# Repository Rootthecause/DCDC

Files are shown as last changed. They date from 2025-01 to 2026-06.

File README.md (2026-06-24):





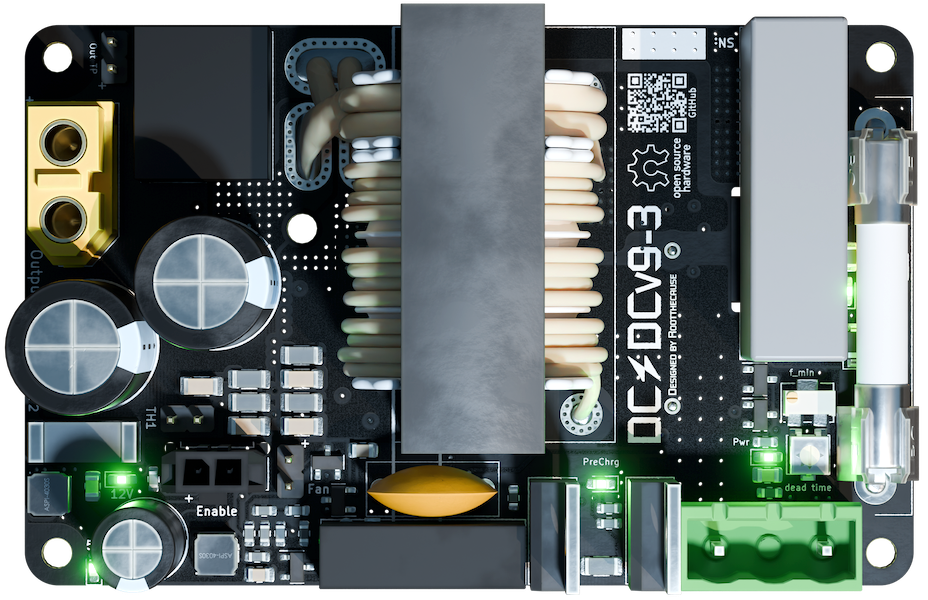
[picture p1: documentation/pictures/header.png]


Dear Formula Student Teams,

I've designed a High Voltage DC/DC Converter to replace our LV Battery. Feel free to use it as well!<br>
Although this design (and previous versions) have passed two times FSG scrutineering and have been operating without any issues for over 6 months, <strong>always manufacture at your own risk!</strong><br>
If you encountered any bugs or have suggestions for improvement, please use the GitHub [issues form](https://github.com/Rootthecause/DCDC/issues/new). For discussions and technical questions, kindly use the [discussion bord](https://github.com/Rootthecause/DCDC/discussions).<br> 

This design is published as open-source hardware under the CERN-OHL-W license and can be found on GitHub: https://github.com/Rootthecause/DCDC<br>
If you had early access to this GitHub page or received any files from me directly, please do not share or publish them, as I don't want others to share files which may be incomplete or contain errors.<br>

Have fun! Do not lick things with spark symbols on :) 

Best regards,
Rootthecause / Liv 

March 10, 2026: Thanks for giving this repro more than 100 stars! ⭐️
<br>

# Updates
### For recent updates on building a v9-3 replica, please read [the v9-3 Build Notes](https://github.com/Rootthecause/DCDC/blob/main/v9-3_build_notes.md).

|Date YYMMDD| Description |
|:---:|:---|
|260609| Added new [v9-4_dev](https://github.com/Rootthecause/DCDC/tree/v9-4_dev) branch. This version is currently untested and not recommended for use. Some components were improved, like D14, U1, U11, Q8, Q9, Q10, Q11. SR FETs have more vias and 20% larger cooling surface. Increased TS side control voltage from 12V to 15V for lower conduction losses.|
|260326 | Update on [v10 development](https://github.com/Rootthecause/DCDC/discussions/9#discussioncomment-16319278) currently being slowed down due to transformer issues |
|260314| Release of the v9-3r1.4 update. Fixes many smaller issues and probably issue #10. See [releases](https://github.com/Rootthecause/DCDC/releases) for more details.|
|260129| First public v10 schematic, see [v10 development](https://github.com/Rootthecause/DCDC/discussions/9#discussioncomment-15634156), also contains a timeline and small v9-3 update|
|260104| New year's update on [v10 development](https://github.com/Rootthecause/DCDC/discussions/9#discussioncomment-15400450) |
|251130| Update on [v10 development](https://github.com/Rootthecause/DCDC/discussions/9#discussioncomment-15114408), added  for faster communication.|
|250915| **IMPORTANT NOTICE**: There was a complaint about the converter not being rules conform. Due to other personal priorities it might take some weeks to solve the addressed points. There is also the chance of some points unable to be resolved for the Version 9-3r. See [issue#10](https://github.com/Rootthecause/DCDC/issues/10) for further details.|
|250806| Announcing the v10 development - ideas welcome! Read more [here](https://github.com/Rootthecause/DCDC/discussions/9). DCDCv10 [survey](https://forms.gle/ou8AZbYJj4cU9K3A8).|
|250718| A bad F_min setting lead to repeatable FET destruction, please re-read the Build Guide Pages 35/36 if you've set up your replica before this change. See [issue#8](https://github.com/Rootthecause/DCDC/issues/8) |
<br>

# Important documents
|File | | |
|:---:|:---:|:---:|
| Documentation [PDF] | [ENGLISH](https://github.com/Rootthecause/DCDC/blob/main/documentation/Documentation_DCDCv9-3r_EN.pdf)| [GERMAN](https://github.com/Rootthecause/DCDC/blob/main/documentation/Documentation_DCDCv9-3r_GER.pdf) [Discontinued*]|
| Build Guide [PDF] | [ENGLISH](https://github.com/Rootthecause/DCDC/blob/main/documentation/Build_Guide_DCDCv9-3r_EN.pdf)| [GERMAN](https://github.com/Rootthecause/DCDC/blob/main/documentation/Build_Guide_DCDCv9-3r_GER.pdf) [Discontinued*]|
| Data sheet [PDF] | [ENGLISH](https://github.com/Rootthecause/DCDC/blob/main/documentation/Datasheet_DCDCv9-3.pdf)|-|
| KiCAD Files| [ENGLISH](https://github.com/Rootthecause/DCDC/tree/main/kicad)|-|
| Schematic [PDF] | [ENGLISH](https://github.com/Rootthecause/DCDC/blob/main/kicad/DCDCv9-3.pdf) |-|
| LTspice Simulation| [ENGLISH](https://github.com/Rootthecause/DCDC/tree/main/ltspice)|-|
| Measurements Table [xlsx] | [ENGLISH](https://github.com/Rootthecause/DCDC/blob/main/documentation/DCDCv9-3_Table.xlsx) |-|
| Scrutineering Support Presentation [PPTX] | [ENGLISH](https://github.com/Rootthecause/DCDC/blob/main/documentation/scrutineering_support_files/DCDCv9-3_Scrutineering_Support_Presentation.pptx)|-|

*will not be updated after the DCDCv9-3r1.4 release (March 14, 2026).

<br>

# Note for PCB-Orders
**Always check the latest release before ordering!**
There are new releases for every significant hardware change.
I do not recommend ordering from the latest repro clone, as it might contain unfinished hardware changes. However, simulation files or documents might be more recent.
<br>
<br>
# Who should build this?
This project is for anyone who is keen to build a DC/DC converter for powering low voltage devices from high voltages or for research.
Unfortunately, it's currently not a simple one-day-build (maybe 1-2 days for building and 1-2 Weeks for testing), but I'm working on it, making it as accessible as possible.
The skillset required ranges from soldering SMD components, SLA-Printing to sanding ferrite cores and winding a transformer (sanding is currently not needed anymore).
The documentation not only contains explanations of many components, but also detailed written assembly instructions.
I might also record a few instruction videos if there is a demand.
Stick with it - the results speak for themselves.<br>
<br>
# Technical Specifications

The DCDCv9-3 is a galvanically isolated DC/DC converter, designed to convert voltages from 200 V to 600 V down to 24 V with max. 500 W continuous output power. The low weight of 167 grams and the small footprint of a credit card (85.6 x 54 mm) are well suited to the automotive industry for supplying low-voltage systems from HV Batteries. The dynamic operating frequency between 90 and 200 kHz ensures high efficiency for various loads as well as good EMI compliance due to the resonant LLC soft switching topology. Customized versions allow output voltages from 12 V to 48 V.
<strong>

- Input Voltage Range: 200 to 600 V 
- Designed Output Voltage: 24 V
- max. Output Power (min. 400V):
	- Continous:&ensp;&ensp;&ensp;&ensp;500 W
	- 180 Seconds:&ensp; 600 W
	- 60 Seconds:&ensp;&ensp;&ensp;750 W
- max. continous Output Power at 200V: 300 W
- max. continous Output Power at 300V: 500 W
- Efficiency up to 96.9 % at 500 W load / 500 V input
- Size: 85.6 x 54 mm x 45 mm
- Weight: 167 grams

Features
- built-in solid-state precharge
- active rectification (NCP4305DMTTWG)
- Galvanically isolated enable pins with self recharging start-up capacitor
- undervoltage, overvoltage and overcurrent protection 
- low no-load power dissipation (7W-9W) 
- cost efficient UCC25600 LLC controller
- reliable 4 A/6 A UCC21520 Gate Driver
- onboard HV- and LV fuses
- minimum isolation distance 4.5 mm (According to rule EV 4.3.6, Table 5, Conformal Coating: 600V DC -> min. 4 mm spacing required)
- optional back side connectors for on-PCB mount 
- NOT FULLY FSG-Rules 2025 conform [September 15, 2025 there was a complaint, see #10 for further information. This may or may not resolved in the future.]
</strong>
<br>
<br>

### Future plans

The main goal of this project is to create a universal approach for safe and efficient conversion of voltages.
At the moment, the converter can accept any input voltage up to at least 600V if UVP/OVP and component
Values are chosen correctly. On the output side, the step-down regulator (65V) is the limiting factors. 
A VIPER06 IC could be used to achieve HV stepdown, or depending on the input voltage, 
the stepdown could be could be shifted to the input side. This could also allow a self-starting converter to 
be used as an SMPS in combination with a PFC. Another approach would be a bidirectional design so that the 
stepdown is on the lower voltage side. Since active rectification is already implemented, bidirectional 
conversion could be possible given the right IC. With the current development and rise of GaN MOSFETs, 
a converter with PCB transformer in the MHz range might also be possible.

# Do's and dont's 
## General
- Not as much as possible, but as much as needed (words from a friend).
- If you don't test to the limits, you don't know where they are.
- Always start with low Voltage/Power and slowly increase it.
- Figure out what measurements and values (step size) are important.
- If issues appear, try to solve them sooner than later - but depending on type, they can be an oppurtunity to test out limits.
- avoid making too many changes at once (except you want to perform multivariant testing), or be sure that the changes do not affect each other

## Project specific
- use short traces for anything that has to switch things (PCB design is complex, than that, but keep wire impedance low as well as parasitics)
- make sure, your gate Driver provides clean on-off signals to the MOSFETs. Otherwise you'll blow them up for sure sooner or later. Use MOSFETs with Kelvin connections if possible (and be sure about their correct wiring).
- Do use Gate driver IC's and not Gate Transformes (they suck). If possible, use Isolated Gate Drivers. Thats a good layer of protection if the half bridge blows up.
- Always have a Thermal Camera at hand. There are relatively cheap options as USB-C accessories for Phones (~250€). I use one from TOPDON with an added maco lens. It's worth every penny, not just for a DC/DC but also other FS Stuff. It will help you to find overloaded components (too hot) or non functioning compontens (no heat). Keep in mind, that there might be thermally reflective surfaces (brushed aluminium is like a mirror!). 
- Use your ears and nose in a quite environment while testing. Many issues can be heard (humming, cracking sounds), and some smelled (too hot component).
- Be sure to add test points to your PCB while developing, which can be acessed via jumper wires or simliar. Do not attempt to measure anything directly with a probe while the converter is running, since a small slip can be enough to ruin the whole converter and maybe even do harm to yourself. 
- use an Oscilloscope with Isolated inputs (alternative use differential probes or an battery powered Oscilloscope) to check signals. 

## Replicas
*Last updated: June 24, 2026*

- At least 4 Formula Student teams are replicating the DCDCv9-3r in 2026  
- At least 4 teams have successfully built and tested the DCDCv9-3r:  
  - TU Graz Racing, Austria, 2025 + 2026
  - Anonymous team, Germany, 2025
  - Anonymous team, Czech, 2025
  - Anonymous team, (modified version), England, 2026
  - Arrabona Racing Team, Hungary, 2026 
<br>

**Want to add your team to this list (publicly or anonymously)?**  
Send me a DM on [Reddit](https://www.reddit.com/user/Rootthecause/). 
Thanks! <br>

## Star History

<a href="https://www.star-history.com/#Rootthecause/dcdc&type=date&legend=bottom-right">
 <picture>
   <source media="(prefers-color-scheme: dark)" srcset="https://api.star-history.com/svg?repos=Rootthecause/dcdc&type=date&theme=dark&legend=bottom-right" />
   <source media="(prefers-color-scheme: light)" srcset="https://api.star-history.com/svg?repos=Rootthecause/dcdc&type=date&legend=bottom-right" />
   Star History Chart
 </picture>
</a>
<br>
<br>

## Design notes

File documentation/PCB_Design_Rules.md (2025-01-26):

This file contains some additional info on the build guide.

# General design rules
- Function over (optical) design
- Mind the power losses:
    - Choose components and topology as efficient as practical.
    - Make current carrying traces/planes as wide as possible for low resistance.
    - Be aware of the physical PCB stackup:
        - How many OZ Copper on which layer?
        - How thick are prepreg and core materials?
    - Mind parasitics (inductive/capacitive) of traces/planes.
    - Allow good thermal sinks for components that generate heat.
- Figure out, what component values are important and add some safety margin.<br>
Buy the cheapest product that fulfils these requirements from an established manufacturer.
- Don't cheap out at components, which are imporant for safety, reliability, efficieny or performance.
- If in doubt ~~leave it out~~ do simulations.
- If simultaions are inaccurate or too time consuming, try building the real thing and probe your signals. But always remember "Wer misst, misst Mist".
- RTFM (exclamation mark)

## Spacing (IPC 2221 B4) and fillet radius
| Potential between two wires | Spacing required outer/inner| Spacing used outer/inner| fillet radius | used for 
|:---:|:---:|:---:|:---:|:---:|
| ≤ 100 V | 0.050 / 0.1 mm | 0.2 / 0.2 mm | 0.5 mm | 24 V and Signals |
| ≤ 150 V | 0.400 / 0.2 mm | 0.4 / 0.2 mm | 1.0 mm | Secondary side rectification |
| ≤ 630 V | 1.197 / 0.575 mm | 1.2 / 0.6 mm | 1.0 mm | HV input |
| any to edge cut | - | 0.3 / 0.3 mm | - | |

## Trace width Rules (IPC 2221)
All currents for 5 k Temp increase @ 1 OZ Copper 
| Trace width  | outer layer | inner layer  |
|:---:|:---:|:---:|
| 0.25 mm | 0.63 A | 0.32 A |
| 0.30 mm | 0.72 A | 0.36 A |
| 0.40 mm | 0.88 A | 0.44 A |
| 0.50 mm | 1.05 A | 0.52 A |
| 0.75 mm | 1.41 A | 0.70 A |
| 1.00 mm | 1.74 A | 0.87 A |
| 1.20 mm | 1.98 A | 0.99 A |
| 2.00 mm | 2.87 A | 1.43 A |
| 3.00 mm | 3.86 A | 1.93 A |
| 4.00 mm | 4.75 A | 2.37 A |
| 5.00 mm | 5.59 A | 2.79 A |

Note: Wider traces may be used to decrease parasitic Inductance and reduce losses.<br>
As a general rule, choose traces as wide as possible for the given space.

## PCB Requirements (for best performance)
- 4-Layer PCB
- 1.6 mm (standard) thickness
- 2 OZ outer Copper, min. 0.5 OZ inner copper (2 OZ for inner layers would be best but are expensive, therefore inner layers are less used for high currents here)
- TG 135 or higher
- matte back PCB Mask performs best for emissivity 
- filled & capped Vias would be best, but plugged ones did not cause any issues so far
- Used Via Size: 0.4 mm hole diameter, 0.8 mm annular ring
- HASL Leaded or unleaded? Both work fine, but for EU better get the unleaded one

## KiCAD Notes
- if the plugin "Fabrication Toolkit" is used, make sure to update pcb from schematic in order to generate an up to date BOM
- special characters like "µ" and "Ω" are not supported by JLC's BOM reader. Be sure to aviod them, otherwise it will be unable to find replacement parts

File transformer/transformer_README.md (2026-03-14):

This file contains some info in addition to the build guide.

Resin used: Liqcreate Flame Retardant HDT 
Link: https://www.liqcreate.com/supportarticles/flame-retardant-hdt-resin-3d/

Notes about shinkage:
All STLs are provided without shinkage compensation. 
Liqcreate's Homepage states 100,65 % Shinkage for X and Y, and 100.50 for Z. 

Here are my own measurements just to check.

ETD39 Isolator (old version before 260309)
| |  X | Y | Z |
|:---:|:---:|:----:|:---:|
|Construction |  41.00 mm |15.00 | 6.00|◊
|Part before curing |  40.93 mm |15.10 | 6.18|
|Part 10 min curing |  40.90 mm |15.10 | 6.20|
|Part 20 min curing |  40.88 mm |15.11 | 6.22|
|Part 30 min curing |  40.88 mm |15.11 | 6.22|
|required compensation|100,29%|99,27%|96,46%|

ETD39 Prim

| |  X | d_innr | d_outr |
|:---:|:---:|:----:|:----:|
|Construction |  21.70 mm |12.90 | 14.90|
|Part before curing |  21.93 mm |12.70 | 14.84|
|Part 10 min curing |  21.91 mm |12.69 | 14.82|
|Part 20 min curing |  21.91 mm |12.69 | 14.81|
|Part 30 min curing |  21.90 mm |12.69 | 14.80|
|required compensation|99,09%|101,65%|100,68%|

ETD39 Sek

| |  X | d_innr | d_outr |
|:---:|:---:|:----:|:----:|
|Construction |  7.00 mm |12.90 | 14.90|
|Part before curing |  7.14 mm * |12.70 | 14.84|
|Part 10 min curing |  7.20 mm |12.71 | 14.79|
|Part 20 min curing |  7.19 mm |12.71 | 14.79|
|Part 30 min curing |  7.18 mm |12.70 | 14.78|
|required compensation|97,49%|101,58%|100,81%|

*unclear what happened there

Transformer Window required: 28,7 mm 
Transformer Window measured: 29,2 mm 

## Conclusion
Somehow some values did not shrink. I believe that the orientation has influence on the shinkage.
But overall, Liqcreate's stated 100,65 % seems plausible. 
I've not conclued any further tests, since the first prints worked well.
Sanding of the flat end-surfaces is allowable if done prior to the isolation test.

## Pro-Tipps
- if you've got too many sticky nots as an promotional gift, use them to stirr your 2K-Epoxy on it. 
- use (left over) PTFE-Tube from a bowden 3D-Printer to stirr the Epoxy. When hardened, it can be easily removed from the tube and be reused.
- you can use hot air (e.g. from a solder station) to warm up deposited epoxy. When warmed, it removes air bubbles in the epoxy and lowers viscosity. This will result in nice surfaces even when the epoxy has started to harden. 
- lay the stirr-tube/rod in the rest of the epoxy. This will give you a good idea how hard the epoxy on the transformer is, without poking it.

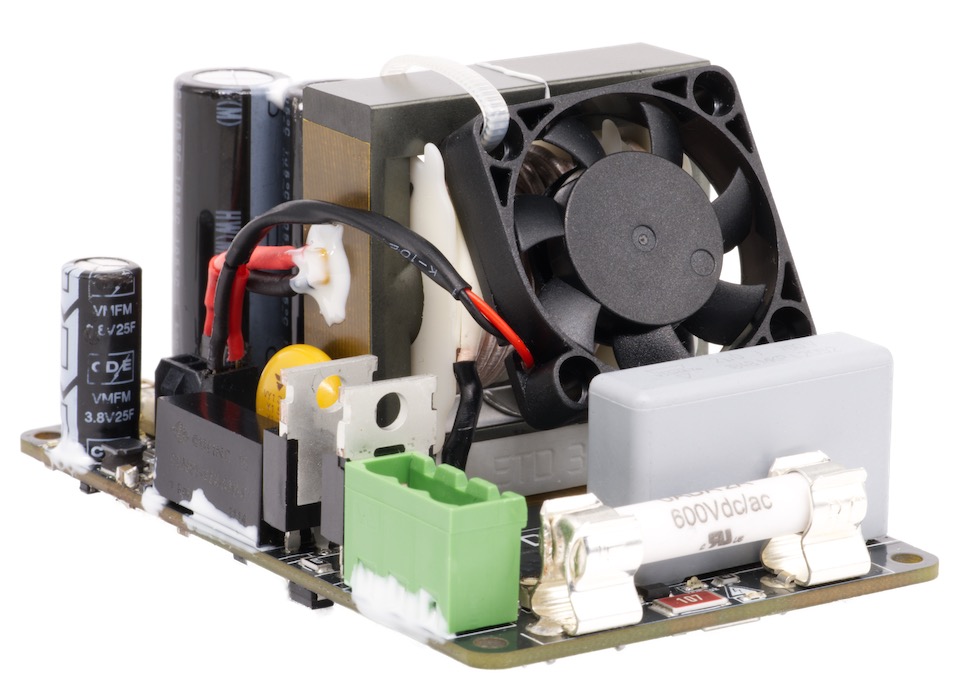
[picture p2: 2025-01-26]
documentation/pictures/DS108936.jpeg

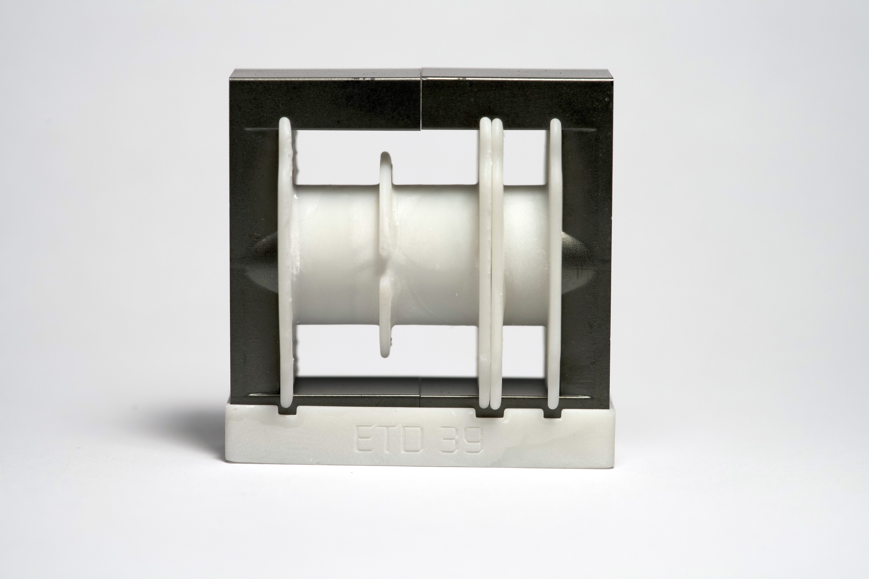
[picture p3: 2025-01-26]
documentation/pictures/DS108508.jpeg

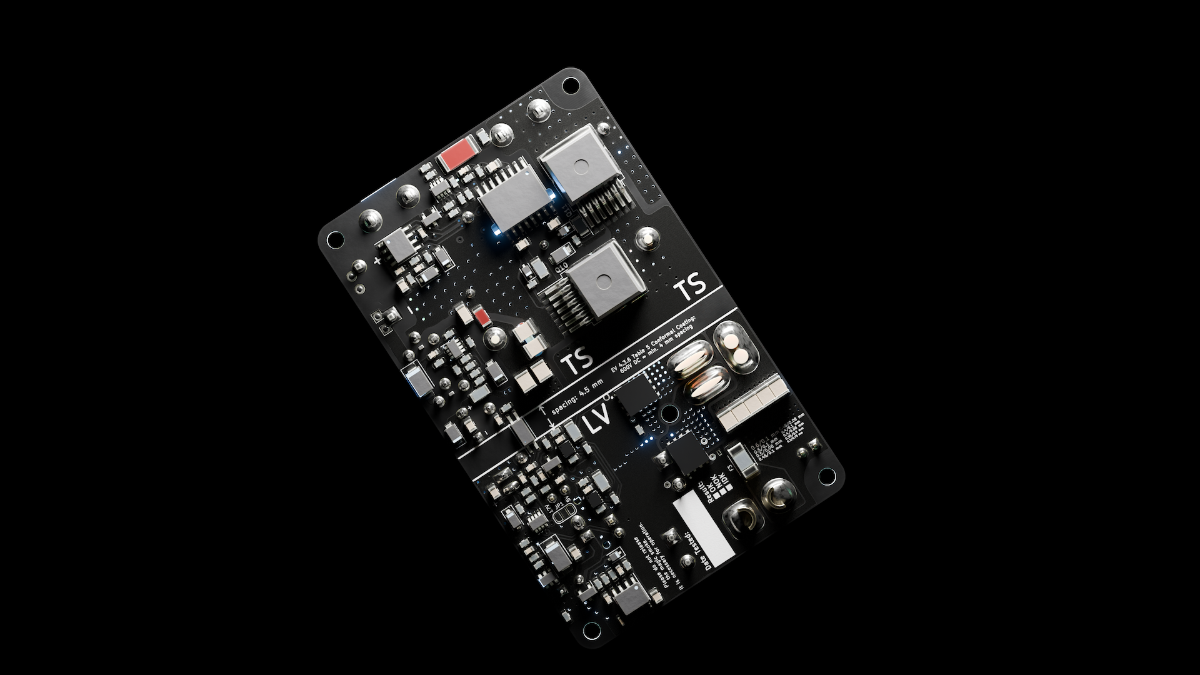
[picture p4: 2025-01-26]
documentation/pictures/bottom.png

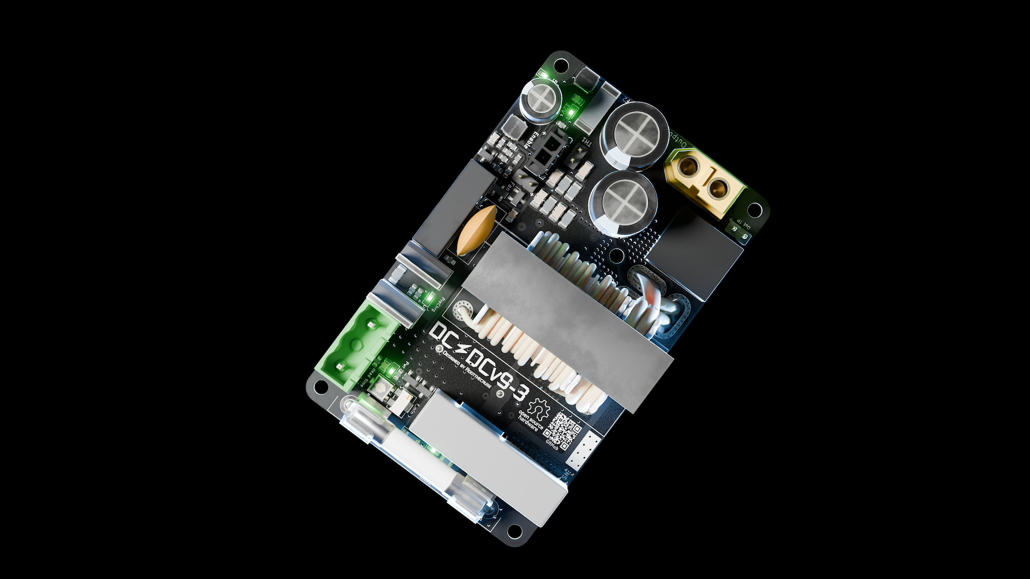
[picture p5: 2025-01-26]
documentation/pictures/top.png

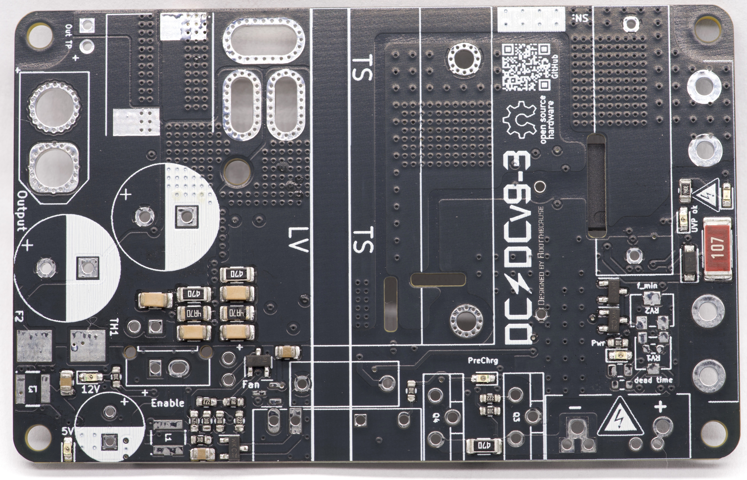
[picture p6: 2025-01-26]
documentation/pictures/DS108613.jpeg

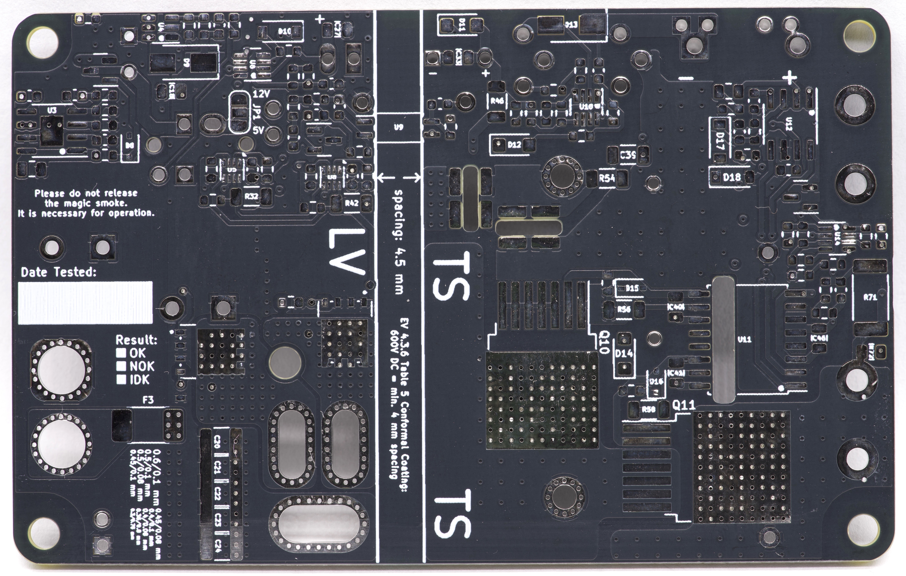
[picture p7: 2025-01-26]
documentation/pictures/DS108614.jpeg

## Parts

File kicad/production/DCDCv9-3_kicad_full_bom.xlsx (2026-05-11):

# | Reference | Value | Datasheet | Manufacturer_Part_Number | Footprint | Qty | ignore for PCBA | ignore for iBOM PCBA | Description | comment | Source
1 | C1 | 2uF | https://www.mouser.de/ProductDetail/Vishay-Roederstein/MKP1848520704K2?qs=i2mp%2Fn9EmlIrcjrkAqMz2A%3D%3D | MKP1848520704K2 | DCDC-Footprints:MKP1848520704K2 | 1 | 1 |  | 2F Film Capacitor 700V Polypropylene (PP), Metallized Radial |  | Mouser
2 | C3 | 22nF | https://www.mouser.de/ProductDetail/80-R76UI22205050J | R76UI22205050J | DCDC-Footprints:R76UI22205050J | 1 | 1 | 1 | R76, Film, Double Metallized Polypropylene, Automotive Grade, 0.022 uF, 5%, 2000 VDC, 85C, Lead Spacing = 15mm |  | Mouser
3 | C4 | 3.3nF | https://www.mouser.de/ProductDetail/Vishay-BC-Components/VY1332M59Y5UQ63V0?qs=YhDfSRCt1jSxb5NtHMih%252Bg%3D%3D | VY1332M59Y5UQ63V0 | DCDC-Footprints:C_Disc_D12.5mm_W5.0mm_P10.00mm | 1 | 1 |  |  |  | Mouser
4 | C29 | 47pF | https://www.mouser.de/ProductDetail/KEMET/C0603C470J1HACTU?qs=sGAEpiMZZMuMW9TJLBQkXvqpoCCiVPPisyfj3y99G5A%3D | C0603C470J1HACTU | DCDC-Footprints:C_0603_1608Metric | 1 |  | 1 |  |  | Mouser
5 | C39 | 470pF | https://www.mouser.de/ProductDetail/Wurth-Elektronik/885342208005?qs=MLItCLRbWswV%252Bu0dQbBqKw%3D%3D | 885342208005 | DCDC-Footprints:C_1206_3216Metric | 1 |  | 1 |  |  | Mouser
6 | C43 | 470nF | https://www.mouser.de/ProductDetail/TAIYO-YUDEN/UMK107ABJ474KA-T?qs=U9dbYxUc11lhcFAuwF4k1w%3D%3D | UMK107ABJ474KA-T | DCDC-Footprints:C_0603_1608Metric | 1 |  | 1 |  |  | Mouser
7 | C11,C13 | 2200uF | https://www.mouser.de/ProductDetail/Nichicon/UHW1V222MHD?qs=Ajmft%252BTTukEyvgC3wSKqgA%3D%3D | UHW1V222MHD | DCDC-Footprints:CP_Radial_D12.5mm_P5.00mm_symbol_inside | 2 | 1 |  |  |  | Mouser
8 | C14,C28 | 100nF | https://www.mouser.de/ProductDetail/TAIYO-YUDEN/HMJ107BB7104KAHT?qs=4JX4e57RtWzHP4tvbkUZyQ%3D%3D | HMJ107BB7104KAHT | DCDC-Footprints:C_0603_1608Metric | 2 |  | 1 |  |  | Mouser
9 | C15,C40,C41 | 2.2uF | https://www.mouser.de/ProductDetail/Samsung-Electro-Mechanics/CL21B225KBYNNWE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 | CL21B225KBYNNWE | DCDC-Footprints:C_0805_2012Metric | 3 |  | 1 |  |  | Mouser
10 | C16,C49,C50,C51,C52,C53,C56,C57 | 1nF | https://www.mouser.de/ProductDetail/Wurth-Elektronik/885342206003 | 885342206003 | DCDC-Footprints:C_0603_1608Metric | 8 |  | 1 |  |  | Mouser
11 | C17,C19,C25,C31,C45 | 1uF | https://www.mouser.de/ProductDetail/187-CL10B105KB8NQNC | CL10B105KB8NQNC | DCDC-Footprints:C_0603_1608Metric | 5 |  | 1 |  |  | Mouser
12 | C20,C21,C22,C23,C24 | 10uF | https://www.mouser.de/ProductDetail/Murata-Electronics/GRM32ER71J106MA12L | GRM32ER71J106MA12L | DCDC-Footprints:C_1210_3225Metric | 5 |  | 1 |  |  | Mouser
13 | C26,C44,C47 | 22nF | https://www.mouser.de/ProductDetail/KEMET/C0603C223K1RAC?qs=6hrdNfwfqM60HSsDbVD%2FNA%3D%3D | C0603C223K1RAC | DCDC-Footprints:C_0603_1608Metric | 3 |  | 1 |  |  | Mouser
14 | C30,C32,C48 | 10nF | https://www.mouser.de/ProductDetail/KEMET/C0603C103K2RECTU?qs=Mv7BduZupUj%2FMy3Zlcu2KQ%3D%3D | C0603C103K2RECTU | DCDC-Footprints:C_0603_1608Metric | 3 |  | 1 |  |  | Mouser
15 | C34,C35,C36,C37 | 5.6nF | https://www.mouser.de/ProductDetail/KEMET/C1210C562JDGACAUTO?qs=By6Nw2ByBD3VuZ7quZlLow%3D%3D | C1210C562JDGACAUTO | DCDC-Footprints:C_1210_3225Metric | 4 | 1 |  |  |  | Mouser
16 | C5,C33,C46 | 10uF | https://www.mouser.de/ProductDetail/Taiyo-Yuden/TMK212BBJ106KG-T?qs=PzICbMaShUdwxQxDcETuPw%3D%3D | TMK212BBJ106KG-T | DCDC-Footprints:C_0805_2012Metric | 3 |  | 1 |  |  | Mouser
17 | C6,C9 | 1 nF | https://www.mouser.de/ProductDetail/Walsin/SH31B102K631CT?qs=ZrPdAQfJ6DPRDGJZHcu%252BNw%3D%3D | SH31B102K631CT | DCDC-Footprints:C_1206_3216Metric | 2 |  | 1 |  |  | Mouser
18 | C8,C12,C18,C27,C42,C54 | 22uF | https://www.mouser.de/ProductDetail/Samsung-Electro-Mechanics/CL21A226MAYNNNE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 | CL21A226MAYNNNE | DCDC-Footprints:C_0805_2012Metric | 6 |  | 1 |  |  | Mouser
19 | C_start1 | 3.8V 25F Supercap | https://www.mouser.de/ProductDetail/Cornell-Dubilier-CDE/VMF256M3R8?qs=eP2BKZSCXI7tEWAxwE24mw%3D%3D | VMF256M3R8 | DCDC-Footprints:CP_Radial_D8.0mm_P3.50mm | 1 | 1 |  |  |  | Mouser
20 | D1 | HV_Orange | https://www.mouser.de/ProductDetail/Kingbright/APTD1608LSECK-J4-PF?qs=6oMev5NRZMEP9SnMY7kNaw%3D%3D | APTD1608LSECK/J4-PF | DCDC-Footprints:LED_0603_1608Metric_Pad1.05x0.95mm_HandSolder | 1 |  | 1 |  |  | Mouser
21 | D11,D12,D14 | VS-E7FX0212-M3/I | https://www.mouser.de/ProductDetail/Vishay/VS-E7FX0212-M3-I | VS-E7FX0212-M3/I | DCDC-Footprints:D_SMF | 3 | 1 |  |  |  | Mouser
22 | D2,D10,D17,D18 | 1N4448 | https://www.mouser.de/ProductDetail/Diodes-Incorporated/1N4448WQ-7-F?qs=s5XU71A7K78gaRcR8oskdg%3D%3D | 1N4448WQ-7-F | DCDC-Footprints:D_SOD-123 | 4 |  | 1 |  |  | Mouser
23 | D3,D4,D5,D6,D7 | Green | https://www.mouser.de/ProductDetail/Inolux/IN-S63AT5G?qs=fAHHVMwC%252Bbiw6WrSEma0zA%3D%3D | IN-S63AT5G | DCDC-Footprints:LED_0603_1608Metric_Pad1.05x0.95mm_HandSolder | 5 |  | 1 |  |  | Mouser
24 | D8,D15,D16 | CDSOD323-T12 | https://www.mouser.de/ProductDetail/Bourns/CDSOD323-T12?qs=N%252BiqXe0%252BQtvMUCyfprYg2w%3D%3D | CDSOD323-T12 | DCDC-Footprints:D_SOD-323 | 3 |  | 1 |  |  | Mouser
25 | D9,D13 | SS1H10 | https://www.mouser.de/ProductDetail/Vishay-General-Semiconductor/SS1H10-M3-61T | SS1H10-M3/61T | DCDC-Footprints:D_SMA | 2 |  | 1 |  |  | Mouser
26 | F1 | 1.6A | https://eu.mouser.com/ProductDetail/Bel-Fuse/0ADBC1600-BE?qs=rrS6PyfT74ehcAOXmfXChA%3D%3D | 0ADBC1600-BE | DCDC-Footprints:Fuseholder0,25Zoll_32mm_littlefuse_102_122 | 1 | 1 |  |  | Install F1.1 and F1.2, Fuse weight: 3.04 g | Mouser
27 | F2 | 500mA | https://www.mouser.de/ProductDetail/Littelfuse/0154.500DR?qs=gu7KAQ731URctJS76sTUdA%3D%3D | 0154.500DR | DCDC-Footprints:NANO-0154-OMNI-BLOK-Fuse-Holder | 1 | 1 |  |  |  | Mouser
28 | F3 | 20A | https://www.mouser.de/ProductDetail/Bel-Fuse/0679L9200-01?qs=ZqXcJfGlKsj4oTNRI%252B0pHw%3D%3D | 0679L9200-01 | DCDC-Footprints:Bel_SMCF_Fuse_2410_6125Metric | 1 | 1 |  |  | Weight: 0.12g | Mouser
29 | F1.1,F1.2 | ~ | https://www.mouser.de/ProductDetail/Littelfuse/01220083Z?qs=95aqoVzNh5YRvw7yc4yLmA%3D%3D | 01220083Z | ~ | 2 |  |  |  |  | Mouser
30 | J1 | 43650-0315 | https://www.mouser.de/ProductDetail/Molex/43650-0315?qs=Nb99Pa9xYq%2FPpvf19i2uYA%3D%3D | 43650-0315 | Samacsys:43650-03YY_151617 | 1 |  |  | Micro-Fit 3.0 Vertical Header, 3.00mm Pitch, Single Row, 3 Circuits, with PCB Polarizing Peg, Glow-Wire Capable, Black
31 | J1.1 | 43645-0300 | https://www.mouser.de/ProductDetail/Molex/43645-0300?qs=W6FIH8d5%2F%2F06ciSdVM35nA%3D%3D | 43645-0300 |  | 1 |  |  | Receptacle Housing
32 | J3 | Conn_01x02 | https://www.mouser.de/ProductDetail/Molex/43650-0215?qs=AplfTeSvkkDe0NAwMnlPNw%3D%3D | 43650-0215 | DCDC-Footprints:Molex_Micro-Fit_3.0_43650-0215_1x02_P3.00mm_Vertical_combined2.54pinheader | 1 | 1 |  |  | switch must handle at least 0.5 A, Do not install if clip-on installation is used, install a 2.54 mm Pin header on the bottom side instead | Mouser
33 | J3.1 | Conn_01x02 | https://www.mouser.de/ProductDetail/Molex/43645-0200?qs=4XSMV6Twtb2TZ7elJDViLw%3D%3D | 43645-0200 |  | 1 | 1 |  | Receptacle Housing | Receptacle Housing | Mouser
34 | J5 | XT60 Male | https://www.amazon.de/RUNCCI%C2%AE-Connector-M%C3%A4nnlich-Weiblich-Rundstecker/dp/B07N1N2C94/ | ~ | DCDC-Footprints:AMASS_XT60-F_1x02_P7.20mm_Vertical | 1 | 1 |  |  | install on the top or bottom depending on normal or clip-on mount | Amazon
35 | J5.1 | XT60 Female (wrong symbol ik) | https://www.amazon.de/RUNCCI%C2%AE-Connector-M%C3%A4nnlich-Weiblich-Rundstecker/dp/B07N1N2C94/ | ~ | ~ | 1 | 1 |  | Female | for connecting your LV System to the DCDC | Amazon
36 | J1.2,J1.3,J1.4,J3.2,J3.3 | Conn_01x01_Pin | https://www.mouser.de/ProductDetail/Molex/43030-0039?qs=Cb2nCFKsA8oKBWEd0s1rng%3D%3D | 43030-0039 | ~ | 5 |  |  | Crimp for molex micofit receptacle housing, 8.5 A
37 | J2,J4,J6,J7,J8 | Conn_01x02_Male | https://www.mouser.de/ProductDetail/Molex/42375-2486?qs=ZGcr3cVYdJDHJgFjWDdRLQ%3D%3D | 42375-2486 | DCDC-Footprints:PinHeader_1x02_P2.54mm_Vertical | 5 | 1 | -- mixed values -- |  |  | Mouser
38 | JP1 | Fan Voltage Select | ~ | ~ | DCDC-Footprints:SolderJumper-3_P1.3mm_Open_RoundedPad1.0x1.5mm_NumberLabels | 1 | 1 |  |  | Bridge the middle pad with solder to one of the outer pads for voltage selection. Standard: 3V7. It's not implied to put a component on here. | -
39 | L1 | 4.7uH | https://www.mouser.de/ProductDetail/ABRACON/ASPI-4030S-4R7M-T?qs=BLmuIjeT3qG3sHpduX34Rg%3D%3D | ASPI-4030S-4R7M-T | DCDC-Footprints:ASPI-4030S | 1 | 1 |  | Fixed Inductors 4.7uH 20% Shielded -40C +125C |  | Mouser
40 | L2 | 1uH | https://www.mouser.de/ProductDetail/Wurth-Elektronik/7443091100?qs=d0WKAl%252BL4KYxr3swIfT6pQ%3D%3D | 7443091100 | DCDC-Footprints:7443091100_v9.2 | 1 | 1 |  |  |  | Mouser
41 | L3 | 10uH | https://www.mouser.de/ProductDetail/ABRACON/ASPI-4030S-100M-T?qs=BLmuIjeT3qH3cD5M%252B06ufg%3D%3D | ASPI-4030S-100M-T | DCDC-Footprints:ASPI-4030S | 1 | 1 |  | Fixed Inductors 10uH 20% Shielded -40C +125C |  | Mouser
42 | M1 | Fan | https://www.amazon.de/gp/product/B071JN6HKM/ | ~ | DCDC-Footprints:PinHeader_1x02_P2.54mm_Vertical | 1 |  |  | Fan |  | Amazon
43 | Q3 | SIHP24N80AE-GE3 | https://www.mouser.de/ProductDetail/Vishay-Siliconix/SIHP24N80AE-GE3?qs=xZ%2FP%252Ba9zWqbBIa%2FWS96zgw%3D%3D | SIHP24N80AE-GE3 | DCDC-Footprints:TO-220-3_Vertical_HV1.2mm | 1 | 1 |  |  |  | Mouser
44 | Q4 | IXYP8N90C3 | https://www.mouser.de/ProductDetail/IXYS/IXYP8N90C3?qs=INK05T%2FwFA2y8W%252BDqn9C%252BA%3D%3D | IXYP8N90C3 | DCDC-Footprints:TO-220-3_Vertical_HV1.2mm | 1 | 1 |  |  |  | Mouser
45 | Q1,Q2,Q5,Q6,Q7 | PMV20ENR | https://www.mouser.de/ProductDetail/771-PMV20ENR | PMV20ENR | DCDC-Footprints:SOT-23 | 5 |  | 1 |  |  | Mouser
46 | Q10,Q11 | IMBG65R050M2HXTMA1 | https://www.mouser.de/ProductDetail/Infineon-Technologies/IMBG65R050M2HXTMA1?qs=mELouGlnn3dkZTVPBkW2JQ%3D%3D | IMBG65R050M2HXTMA1 | DCDC-Footprints:TO-263-7_TabPin8 | 2 | 1 |  |  |  | Mouser
47 | Q8,Q9 | BSC027N06LS5ATMA1 | https://www.mouser.de/ProductDetail/Infineon-Technologies/BSC027N06LS5ATMA1?qs=HXFqYaX1Q2z6vEIhZX7Vzw%3D%3D | BSC027N06LS5ATMA1 | DCDC-Footprints:BSC027N06LS5ATMA1 | 2 |  | 1 | MOSFET DIFFERENTIATED MOSFETS |  | Mouser
48 | R6 | 47 | https://www.mouser.de/ProductDetail/Panasonic/ERJ-P08J470V?qs=Zyl8A9hlmJqxO%2F4JKlaR%2FA%3D%3D | ERJ-P08J470V | DCDC-Footprints:R_1206_3216Metric | 1 |  | 1 |  |  | Mouser
49 | R12 | 910 | https://www.mouser.de/ProductDetail/Bourns/CR0603-FX-9100ELF?qs=Ody%252BWaR0NcGmCng90W%252BU9Q%3D%3D | CR0603-FX-9100ELF | DCDC-Footprints:R_0603_1608Metric | 1 |  | 1 |  |  | Mouser
50 | R25 | 240k | https://www.mouser.de/ProductDetail/YAGEO/AC0603FR-07240KL?qs=yhV1fb9g%2FKZczpBjcR9dXw%3D%3D | AC0603FR-07240KL | DCDC-Footprints:R_0603_1608Metric | 1 |  | 1 |  |  | Mouser
51 | R35 | 330k | https://www.mouser.de/ProductDetail/YAGEO/AC0603JR-07330KL?qs=ygRr%2FtkhteswRX2BvSPS%2Fg%3D%3D | AC0603JR-07330KL | DCDC-Footprints:R_0603_1608Metric | 1 |  | 1 |  | Voltage Divider with R36 and TH2 | Mouser
52 | R37 | 47k | https://www.mouser.de/ProductDetail/YAGEO/RC0603FR-0747KL?qs=gt6vzsuosg3jXzmCiDCCdg%3D%3D | RC0603FR-0747KL | DCDC-Footprints:R_0603_1608Metric | 1 |  | 1 |  | Slow lane resonse. R37 and C26 will act as LC-Filter. Larger values will increase response time | Mouser
53 | R44 | 510 | https://www.mouser.de/ProductDetail/Vishay-Dale/CRCW0603510RFKEBC?qs=wd5RIQLrsJguodz6NSuy6g%3D%3D | CRCW0603510RFKEBC | DCDC-Footprints:R_0603_1608Metric | 1 |  | 1 |  | limits the maximum switching frequency. Higher value will decrease max. switching frequncy. If set below appx. 680Ω the max. f_sw is set above 350 kHz which results in burst mode. | Mouser
54 | R46 | 20 | https://www.mouser.de/ProductDetail/Bourns/CR1206-FX-20R0ELF?qs=sGAEpiMZZMtlubZbdhIBIPXF8FEETpZcqCEELkhp6xo%3D | CR1206-FX-20R0ELF | DCDC-Footprints:R_1206_3216Metric | 1 |  | 1 |  | current limiting for D14. Current is roughtly 12V/R46 | Mouser
55 | R54 | 10M | https://www.mouser.de/ProductDetail/Bourns/CHV1206-JW-106ELF?qs=m3kjewahW8RqgYkeeJasig%3D%3D | CHV1206-JW-106ELF | DCDC-Footprints:R_1206_3216Metric | 1 |  | 1 |  | current limiting | Mouser
56 | R60 | 82k | https://www.mouser.de/ProductDetail/YAGEO/RC0603JR-0782KL?qs=sGAEpiMZZMtlubZbdhIBIAVdtiC5pVGKjg4gTFnK6BA%3D | RC0603JR-0782KL | DCDC-Footprints:R_0603_1608Metric | 1 |  | 1 |  | OC discharge, lower resistance will allow for higher Cr Voltage | Mouser
57 | R64 | 820k | https://www.mouser.de/ProductDetail/Bourns/CR0603-FX-8203ELF?qs=Ody%252BWaR0NcFwghMO7RilRQ%3D%3D | CR0603-FX-8203ELF | DCDC-Footprints:R_0603_1608Metric | 1 |  | 1 |  | set hysteresis with R62 | Mouser
58 | R65 | 510k | https://www.mouser.de/ProductDetail/Bourns/CR0603-JW-514ELF?qs=tknLyCMIRbO2DmI%2FxH6p%2Fg%3D%3D | CR0603-JW-514ELF | DCDC-Footprints:R_0603_1608Metric | 1 |  | 1 |  | Voltage divider with R66 and R1 | Mouser
59 | R68 | 1.6M | https://www.mouser.de/ProductDetail/YAGEO/AC0603FR-071M6L?qs=ygRr%2Ftkhtesuj8RqEBImQQ%3D%3D | AC0603FR-071M6L | DCDC-Footprints:R_0603_1608Metric | 1 |  | 1 |  | voltage divider with R67 and R71 | Mouser
60 | R75 | 100k | https://www.mouser.de/ProductDetail/ROHM-Semiconductor/ESR03EZPJ104?qs=493kPxzlxfLd9svH5sC01g%3D%3D | ESR03EZPJ104 | Resistor_SMD:R_0603_1608Metric | 1 |  | 1 |  | Note: R75 is currently not on the PCB and must be soldered on top of R31. | Mouser
61 | R1,R71 | 100M | https://www.mouser.de/ProductDetail/Bourns/CHV2512-JW-107ELF?qs=m3kjewahW8Spv95Ja3mjwQ%3D%3D | CHV2512-JW-107ELF | DCDC-Footprints:R_2512_6332Metric_Pad1.40x3.35mm_HandSolder | 2 |  | 1 |  |  | Mouser
62 | R13,R19 | 100 | https://www.mouser.de/ProductDetail/YAGEO/RC1206JR-7W100RL | RC1206JR-7W100RL | DCDC-Footprints:R_1206_3216Metric | 2 |  | 1 |  |  | Mouser
63 | R17,R24 | 27k | https://www.mouser.de/ProductDetail/Bourns/CR0603-JW-273ELF?qs=QNvGIbmBFecjQAhNwzrFog%3D%3D | CR0603-JW-273ELF | DCDC-Footprints:R_0603_1608Metric | 2 |  | 1 |  |  | Mouser
64 | R18,R27,R50 | 470k | https://www.mouser.de/ProductDetail/Vishay-Dale/RCS0603470KJNEA?qs=NKmfXavxMazYXJw1HCoZ6Q%3D%3D | RCS0603470KJNEA | DCDC-Footprints:R_0603_1608Metric | 3 |  | 1 |  |  | Mouser
65 | R2,R72 | 330k | https://www.mouser.de/ProductDetail/Panasonic/ERJ-P06J334V?qs=Zyl8A9hlmJqi95c7ry13cQ%3D%3D | ERJ-P06J334V | DCDC-Footprints:R_0805_2012Metric | 2 |  | 1 |  |  | Mouser
66 | R26,R45,R47,R53,R67,R70 | 100k | https://www.mouser.de/ProductDetail/ROHM-Semiconductor/ESR03EZPJ104?qs=493kPxzlxfLd9svH5sC01g%3D%3D | ESR03EZPJ104 | DCDC-Footprints:R_0603_1608Metric | 6 |  | 1 |  | -- mixed values -- | Mouser
67 | R28,R34,R66 | 33k | https://www.mouser.de/ProductDetail/YAGEO/AC0603FR-0733KL?qs=UoPT7wUmgYIYAFR3BAARQg%3D%3D | AC0603FR-0733KL | DCDC-Footprints:R_0603_1608Metric | 3 |  | 1 |  | -- mixed values -- | Mouser
68 | R31,R36 | 4.7k | https://www.mouser.de/ProductDetail/Vishay-Dale/CRCW06034K70FKEC?qs=L%252B14cgJd8NPi5InG5zfNWw%3D%3D | CRCW06034K70FKEC | DCDC-Footprints:R_0603_1608Metric | 2 |  | 1 |  |  | Mouser
69 | R32,R42 | 4.7 | https://www.mouser.de/ProductDetail/Panasonic/ERJ-P08J4R7V?qs=sGAEpiMZZMtlubZbdhIBIK7FbVYKWV6WtRy9y9o9OQM%3D | ERJ-P08J4R7V | DCDC-Footprints:R_1206_3216Metric | 2 |  | 1 |  | Gate current limiter. Smaller values will lower switching times, but might increase ringing | Mouser
70 | R39,R41,R59,R61 | 1k | https://www.mouser.de/ProductDetail/ROHM-Semiconductor/ESR03EZPJ102?qs=DyUWGjl%252BcVvjMuV%252BzioV7Q%3D%3D | ESR03EZPJ102 | DCDC-Footprints:R_0603_1608Metric | 4 |  | 1 |  |  | Mouser
71 | R5,R7,R9,R11,R15,R16,R21,R23,R30,R33,R40,R43,R51,R52,R55,R57,R63 | 10k | https://www.mouser.de/ProductDetail/ROHM-Semiconductor/ESR03EZPJ103?qs=DyUWGjl%252BcVt8C23uz7MWdg%3D%3D | ESR03EZPJ103 | DCDC-Footprints:R_0603_1608Metric | 17 |  | 1 |  |  | Mouser
72 | R56,R58 | 10 | https://www.mouser.de/ProductDetail/YAGEO/RC1206FR-7W10RL?qs=tggtontpCXM7RQCPv1SaRw%3D%3D | RC1206FR-7W10RL | DCDC-Footprints:R_1206_3216Metric | 2 |  | 1 |  | Gate current limiter. Smaller values will lower switching times, but might increase ringing | Mouser
73 | R62,R69 | 100M | https://www.mouser.de/ProductDetail/Vishay-Dale/CRCW0603100MJPEAHR?qs=DhCTQV%252BB7kX%252B%2FzChlJdsfw%3D%3D | CRCW0603100MJPEAHR | DCDC-Footprints:R_0603_1608Metric | 2 |  | 1 |  | set hysteresis | Mouser
74 | R73,R74 | 10 | https://www.mouser.de/ProductDetail/Panasonic/ERJ-PA3J100V?qs=sGAEpiMZZMtlubZbdhIBIL24R7XL4VFW3x7wh7xo8eA%3D | ERJ-PA3J100V | DCDC-Footprints:R_0603_1608Metric | 2 |  | 1 |  |  | Mouser
75 | R8,R10,R22,R29,R38,R48,R49 | 2.2k | https://www.mouser.de/ProductDetail/ROHM-Semiconductor/ESR03EZPJ222?qs=DyUWGjl%252BcVuZfLe1fBr0Mg%3D%3D | ESR03EZPJ222 | DCDC-Footprints:R_0603_1608Metric | 7 |  | 1 |  |  | Mouser
76 | RV1 | 20k | https://www.mouser.de/ProductDetail/Bourns/PVG3A203C01R00?qs=M0b1YOHIqsZb%2F1dv5x4oHQ%3D%3D | PVG3A203C01R00 | DCDC-Footprints:Potentiometer_Bourns_PVG3G | 1 |  |  |  | set dead time, R3 can be used for a fixed value. Read Build guide chapter 8.9 for the correct setting. | Mouser
77 | RV2 | 10k | https://www.mouser.de/ProductDetail/Bourns/PVG5A103C03R00?qs=sGAEpiMZZMu2vyeiTNtwLAWWg9f2DNsdEVwpuMgEBVs%3D | PVG5A103C03R00 | DCDC-Footprints:Potentiometer_Bourns_3214W_Vertical | 1 |  |  |  | Used to set minimum switching frequency. Read Build guide chapter 8.8 for the correct setting. | Mouser
78 | T1 | DIY Transformer ETD 39 | https://www.mouser.de/ProductDetail/EPCOS-TDK/B66363G0000X197?qs=Uha62PnlbFA7ulJ0dmnJ%252BQ%3D%3D | B66363G0000X197 | DCDC-Footprints:Transformer_ETD39_uprightV3.6 (PSS 24V) | 1 |  |  |  | Read Build guide chapter 5 for more info. | Mouser
79 | T1.1 | Ferrite Core | https://www.mouser.de/ProductDetail/871-B66363GX197 | B66363G0000X197 | ~ | 1 | 1 |  | N97 Core without air gap | N97 Core without air gap | Mouser
80 | T1.2 | Ferrite Core (gapped) | https://www.mouser.de/ProductDetail/EPCOS-TDK/B66363G1000X127?qs=wDNl1cNI0GtCaGtNmNbDKg%3D%3D | B66363G1000X127 | ~ | 1 | 1 |  | N97 Core without air gap | N97 Core without air gap | Mouser
81 | T1.3 | 1800 mm 120 x 0.1 mm HF litz wire (Prim) | https://www.ebay.de/itm/304154052959?_skw=hf+litze&itmmeta=01J9STH5QCVFSQVBEJX5R17A6A&var=604128480922 | 120 x 0.1 mm | ~ | 1 | 1 |  | Inductor, rotated by 45° | HF litz wire | Ebay
82 | T1.4,T1.5 | 165 mm 600 x 0,071 mm HF litz wire (inner Sec) | https://www.ebay.de/itm/304154052959?_skw=hf+litze&itmmeta=01J9STH5QCVFSQVBEJX5R17A6A&var=604128480922 | 120 x 0.1 mm | ~ | 2 | 1 |  | Inductor, rotated by 45° | HF litz wire | Ebay
83 | TH1 | 3.9k PTC (read build guide!) | https://www.mouser.de/ProductDetail/Vishay-Dale/TFPTL15L3901FL2B?qs=EYbNv5wfoHs1U3qiZRAw9A%3D%3D | TFPTL15L3901FL2B | DCDC-Footprints:PinHeader_1x02_P2.54mm_Vertical | 1 | 1 |  |  | if disconnected, fan will be on permanently (can be a desired feature), mount according to build guide | Mouser
84 | TH2 | 1k PTC | https://www.mouser.de/ProductDetail/Vishay-Dale/TFPT0603L1001DV?qs=8wHch9UpSvbyFTWmCyxuaA%3D%3D | TFPT0603L1001DV | DCDC-Footprints:R_0603_1608Metric | 1 | 1 |  |  | max. 1 kΩ for 0603 size available, but higher resistance would be better for SNR and lower current | Mouser
85 | U1 | RP-1212S | https://www.mouser.de/ProductDetail/RECOM-Power/RP-1212S?qs=YWgezujkI1KjTZkjNYMtQA%3D%3D | RP-1212S | DCDC-Footprints:Converter_DCDC_TRACO_TBA 1-1212HI-3kV-iso | 1 | 1 |  |  |  | Mouser
86 | U2 | RT9058-90GVL | https://www.mouser.de/ProductDetail/Richtek/RT9058-90GVL?qs=amGC7iS6iy%2FmB38%252BYpIKLg%3D%3D | RT9058-90GVL | DCDC-Footprints:SOT-23 | 1 | 1 |  | 250mA Low Quiscent Current LDO, 1.8V output, SOT-23 |  | Mouser
87 | U3 | MP4541_SOP8-EP | https://www.mouser.de/ProductDetail/Monolithic-Power-Systems-MPS/MP4541GN-Z?qs=TCDPyi3sCW3JrMFxnpK4AA%3D%3D | MP4541GN-Z | DCDC-Footprints:SOIC-8-1EP_3.9x4.9mm_P1.27mm_EP2.29x3mm XL7005 | 1 | 1 |  |  |  | Mouser
88 | U4 | TLV61048DBVR | https://www.mouser.de/ProductDetail/595-TLV61048DBVR | TLV61048DBVR | DCDC-Footprints:SOT-23-6 | 1 |  | 1 |  |  | Mouser
89 | U7 | TL431BCDBZR | https://www.mouser.de/ProductDetail/Texas-Instruments/TL431BCDBZRG4?qs=odmYgEirbwyei9%252B4Lesgiw%3D%3D | TL431BCDBZRG4 | DCDC-Footprints:SOT-23 | 1 |  | 1 |  | integrated opamp with 2.5V reference souce. Acts somewhat like a Zener diode | Mouser
90 | U9 | ACPL-217-50AE | https://www.mouser.de/ProductDetail/Broadcom-Avago/ACPL-217-50AE?qs=dcm2zoLQumB4Kh%252BCZrN57A%3D%3D | ACPL-217-560E | DCDC-Footprints:SOIC-4_4.55x2.6mm_P1.27mm | 1 |  | 1 |  | optocoupler for isolated voltage control loop. Note: If different type or CRT is used, the gain (R41) may need to be changed | Mouser
91 | U11 | UCC21520DW | https://www.mouser.de/ProductDetail/Texas-Instruments/UCC21520DW?qs=zEmsApcVOkX3g4f0E3%252BNKw%3D%3D | UCC21520DW | DCDC-Footprints:SOIC-16W_7.5x10.3mm_P1.27mm | 1 |  | 1 |  | isolated gate driver, see datasheet for more info | Mouser
92 | U12 | UCC25600 | https://www.mouser.de/ProductDetail/Texas-Instruments/UCC25600DR?qs=drm0CCHqiV642WXShX2ZHQ%3D%3D | UCC25600DR | DCDC-Footprints:SOIC-8_3.9x4.9mm_P1.27mm | 1 |  | 1 |  | Main control IC, see datasheet for more info | Mouser
93 | U13 | ZXRE330ASA-7 | https://www.mouser.de/ProductDetail/Diodes-Incorporated/ZXRE330ASA-7?qs=4q%2FTN4Rqj6JkCriwoAvbDA%3D%3D | ZXRE330ASA-7 | DCDC-Footprints:SOT-23 | 1 | 1 |  |  | Used as low current voltage reference, normal LDO would be fine too. | Mouser
94 | U5,U8 | NCP4305DMTTWG | https://www.mouser.de/ProductDetail/onsemi/NCP4305DMTTWG?qs=8hV9pjh0QhMP%252BMQhCLTuGQ%3D%3D | NCP4305DMTTWG | DCDC-Footprints:WDFN-8_2x2mm_P0.5mm | 2 | 1 |  |  |  | Mouser
95 | U6,U10,U14 | LM2904BIDDFR | https://www.mouser.de/ProductDetail/595-LM2904BIDDFR | LM2904BIDDFR | DCDC-Footprints:SOT-23-8_DC-DC_v9 | 3 |  | 1 |  |  | Mouser

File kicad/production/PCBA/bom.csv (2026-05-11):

Designator | Footprint | Quantity | Value | LCSC Part #
C1 | MKP1848520704K2 | 1 | 2uF
C11, C13 | CP_Radial_D12.5mm_P5.00mm_symbol_inside | 2 | 2200uF
C12, C18, C27, C42, C54, C8 | 0805 | 6 | 22uF
C14, C28 | 0603 | 2 | 100nF
C15, C40, C41 | 0805 | 3 | 2.2uF
C16, C49, C50, C51, C52, C53, C56, C57 | 0603 | 8 | 1nF
C17, C19, C25, C31, C45 | 0603 | 5 | 1uF
C20, C21, C22, C23, C24 | 1210 | 5 | 10uF
C26, C44, C47 | 0603 | 3 | 22nF
C29 | 0603 | 1 | 47pF
C30, C32, C48 | 0603 | 3 | 10nF
C33, C46, C5 | 0805 | 3 | 10uF
C34, C35, C36, C37 | 1210 | 4 | 5.6nF
C39 | 1206 | 1 | 470pF
C4 | C_Disc_D12.5mm_W5.0mm_P10.00mm | 1 | 3.3nF
C43 | 0603 | 1 | 470nF
C6, C9 | 1206 | 2 | 1 nF
C_START1 | CP_Radial_D8.0mm_P3.50mm | 1 | 3.8V 25F Supercap
D1 | 0603 | 1 | HV_Orange
D10, D17, D18, D2 | D_SOD-123 | 4 | 1N4448
D11, D12, D14 | D_SMF | 3 | VS-E7FX0212-M3/I
D13, D9 | D_SMA | 2 | SS1H10
D15, D16, D8 | D_SOD-323 | 3 | CDSOD323-T12
D3, D4, D5, D6, D7 | 0603 | 5 | Green
F1 | Fuseholder0,25Zoll_32mm_littlefuse_102_122 | 1 | 1.6A
F2 | NANO-0154-OMNI-BLOK-Fuse-Holder | 1 | 500mA
F3 | Bel_SMCF_Fuse_2410_6125Metric | 1 | 20A
J1 | 43650-03YY_151617 | 1 | 43650-0315
J2, J4, J8 | PinHeader_1x02_P2.54mm_Vertical | 3 | Conn_01x02_Male
J3 | Molex_Micro-Fit_3.0_43650-0215_1x02_P3.00mm_Vertical_combined2.54pinheader | 1 | Conn_01x02
J5 | AMASS_XT60-F_1x02_P7.20mm_Vertical | 1 | XT60 Male
JP1 | SolderJumper-3_P1.3mm_Open_RoundedPad1.0x1.5mm_NumberLabels | 1 | Fan Voltage Select
L1 | ASPI-4030S | 1 | 4.7uH
L2 | 7443091100_v9.2 | 1 | 1uH
L3 | ASPI-4030S | 1 | 10uH
Q1, Q2, Q5, Q6, Q7 | SOT-23 | 5 | PMV20ENR
Q10, Q11 | TO-263-7_TabPin8 | 2 | IMBG65R050M2HXTMA1
Q3 | TO-220-3_Vertical_HV1.2mm | 1 | SIHP24N80AE-GE3
Q4 | TO-220-3_Vertical_HV1.2mm | 1 | IXYP8N90C3
Q8, Q9 | BSC027N06LS5ATMA1 | 2 | BSC027N06LS5ATMA1
R1, R71 | 2512 | 2 | 100M
R10, R22, R29, R38, R48, R49, R8 | 0603 | 7 | 2.2k
R11, R15, R16, R21, R23, R30, R33, R40, R43, R5, R51, R52, R55, R57, R63, R7, R9 | 0603 | 17 | 10k
R12 | 0603 | 1 | 910
R13, R19 | 1206 | 2 | 100
R17, R24 | 0603 | 2 | 27k
R18, R27, R50 | 0603 | 3 | 470k
R2, R72 | 0805 | 2 | 330k
R25 | 0603 | 1 | 240k
R26, R45, R47, R53, R67, R70, R75 | 0603 | 7 | 100k
R28, R34, R66 | 0603 | 3 | 33k
R31, R36 | 0603 | 2 | 4.7k
R32, R42 | 1206 | 2 | 4.7
R35 | 0603 | 1 | 330k
R37 | 0603 | 1 | 47k
R39, R41, R59, R61 | 0603 | 4 | 1k
R44 | 0603 | 1 | 510
R46 | 1206 | 1 | 20
R54 | 1206 | 1 | 10M
R56, R58 | 1206 | 2 | 10
R6 | 1206 | 1 | 47
R60 | 0603 | 1 | 82k
R62, R69 | 0603 | 2 | 100M
R64 | 0603 | 1 | 820k
R65 | 0603 | 1 | 510k
R68 | 0603 | 1 | 1.6M
R73, R74 | 0603 | 2 | 10
RV1 | Potentiometer_Bourns_PVG3G | 1 | 20k
RV2 | Potentiometer_Bourns_3214W_Vertical | 1 | 10k
T1 | Transformer_ETD39_uprightV3.6 (PSS 24V) | 1 | DIY Transformer ETD 39
TH2 | 0603 | 1 | 1k PTC
U1 | Converter_DCDC_TRACO_TBA 1-1212HI-3kV-iso | 1 | RP-1212S
U10, U14, U6 | SOT-23-8_DC-DC_v9 | 3 | LM2904BIDDFR
U11 | SOIC-16W_7.5x10.3mm_P1.27mm | 1 | UCC21520DW
U12 | SOIC-8_3.9x4.9mm_P1.27mm | 1 | UCC25600
U13 | SOT-23 | 1 | ZXRE330ASA-7
U2 | SOT-23 | 1 | RT9058-90GVL
U3 | SOIC-8-1EP_3.9x4.9mm_P1.27mm_EP2.29x3mm XL7005 | 1 | MP4541_SOP8-EP
U4 | SOT-23-6 | 1 | TLV61048DBVR
U5, U8 | WDFN-8_2x2mm_P0.5mm | 2 | NCP4305DMTTWG
U7 | SOT-23 | 1 | TL431BCDBZR
U9 | SOIC-4_4.55x2.6mm_P1.27mm | 1 | ACPL-217-50AE

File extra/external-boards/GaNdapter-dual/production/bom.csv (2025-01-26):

Designator | Footprint | Quantity | Value | LCSC Part #
_3, _2, |  | 3
D1, D2 | SBR10U200P513 | 2 | SBR10U200P5-13
Q3, Q4 | GAN3R2100CBEAZ | 2 | GAN3R2-100CBEAZ
TP1, TP11 | GanDapter Long pad | 2 | TestPoint
TP12, TP13, TP14, TP3 | GanDapter single pad | 4 | TestPoint
TP2, TP5 | GanDapter short pad | 2 | TestPoint

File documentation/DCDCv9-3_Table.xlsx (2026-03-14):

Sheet: Notes
DCDCv9-3 Table
GitHub: https://github.com/Rootthecause/DCDC
Date: | 260314
Dear user! The author is not liable for any damages in connection with this document, nor does he guarantee the functionality or correctness of the formulas and measurements described. Use is at your own risk!
This document was created in Google Sheets. The design and functions may vary if a different application used is used.
Found an error? Please submit an Issue on GitHub. Thanks a lot! (https://github.com/Rootthecause/DCDC/issues)
Revision History (YYMMDD)
260314 | probably smaller changes, just a fresh export. Will fully change to YYMMDD on this document soon too.
250702 | rewording of "Input current with fully charged capacitor, 24V_in, Enabled" also changed in the essential checklist.
250522 | Unified date format to DD.MM.YY , renamed 24V_in on the output side to 24V output, assigned 12.2V to the LV side, changed color from green to orange in the Measurements Table for optional measurements, fixed capacitor loss calculator (results where too high by a factor of 2)
250520 | Added Revision History, Added Cstart1 (Internenal Power Supply) storage time and voltage after this time

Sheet: Checklist v9-3
 | Checklist DCDCv9-3 | Identifier for Oscilloscope Screenshots: C | Test passed | 199 | of | 199 | 100.00% | tests done
Essential | Module | Parameter | Value | Unit |  |  | Date | Status | Comment
x | Start-up Cap Supply | Charging Voltage (with C_start), DC/DC Disabled | 3.71 | V | min. 3,5 | max. 3,8 | 2024-10-31 | OK | Constant above 7 V_in (which is the Voltage on the output connector)
 | Start-up Cap Supply | Charging Voltage (with C_start), DC/DC Enabled, U_in = 600 V, IDLE, 5V Fan OFF | 3.69 | V | min. 3,5 | max. 3,8 | 2024-11-28 | OK
 | Start-up Cap Supply | Charging Voltage (with C_start), DC/DC Enabled, U_in = 600 V, IDLE, 5V Fan ON | 3.68 | V | min. 3,5 | max. 3,8 | 2024-11-28 | OK
 | Start-up Cap Supply | Capacitor Shipping Voltage | 3.65 | V | min. 3,5 | max. 3,8 | 2024-11-01 | OK
 | Start-up Cap Supply | Input current with fully charged capacitor, 24V output, Disabled | 1.05 | mA |  |  | 2024-11-01 | OK
x | Start-up Cap Supply | Input current with fully charged capacitor, 24V output, Enabled | 22.3 | mA |  |  | 2025-01-07 | OK
 | Start-up Cap Supply | Input current with fully charged capacitor, 24V output, Enabled, with 5V Fan, 21°C RT | 50 | mA |  |  | 2025-01-07 | OK
x | Start-up Cap Supply | Discharge Current (DC/DC Enabled) no HV, Cap @ 3,70 V | 101 | mA |  |  | 2024-11-01 | OK
 | Start-up Cap Supply | Discharge Current (DC/DC Enabled) 200 V | 198 | mA |  |  | 2024-11-27 | OK
 | Start-up Cap Supply | Discharge Current (DC/DC Enabled) 300 V | 207 | mA |  |  | 2024-11-27 | OK
 | Start-up Cap Supply | Discharge Current (DC/DC Enabled) 400 V | 219 | mA |  |  | 2024-11-27 | OK
 | Start-up Cap Supply | Discharge Current (DC/DC Enabled) 500 V | 236 | mA |  |  | 2024-11-27 | OK
x | Start-up Cap Supply | Discharge Current (DC/DC Enabled) 600 V | 215 | mA |  |  | 2024-11-27 | OK
x | Start-up Cap Supply | Hold-Up time, DC/DC Enabled, no HV | 114 | s |  |  | 2024-11-01 | OK
 | Start-up Cap Supply | Hold-Up time, DC/DC Disbaled | > 6 | months |  |  | 2025-05-20 | OK | after 6 Months of not in use ~20 mV reduction, probably fine for >12 Months.
 | Start-up Cap Supply | Voltage after 6 months, DC/DC Disabled | 3.676 | V |  |  | 2025-05-20 | OK
 | Start-up Cap Supply | 5V LED / step-down turn off input voltage | 3.5 | V |  |  | 2024-11-01 | OK
 | Start-up Cap Supply | 5V LED / step-down turn off time by discharging C11+C13 from 24V, no load, | 172 | s |  |  | 2024-11-01 | OK
 | Step-Up UVLO | must be above min. C_start voltage | 2.535 | V | min. 2,5 | max. 3 | 2024-10-31 | OK but improveable | without C_start: 2,45 V.
 | LV Voltage LV Side Current | U_in = 0 V / DC/DC Enabled, IDLE, 12.2 V LV | 27.8 | mA |  |  | 2025-01-07 | OK
x | LV Voltage LV Side Voltage | U_in = 0 V / DC/DC Enabled, IDLE | 12.204 | V |  |  | 2024-10-31 | OK
x | LV Voltage 9 V LDO | U_in = 0 V / DC/DC Enabled, IDLE, 12.2 V LV, 20,1°C RT | 9.055 | V |  |  | 2024-10-31 | OK
x | LV Voltage, HV Side | U_in = 0 V / DC/DC Enabled, IDLE, 12.2 V LV | 12.475 | V |  |  | 2024-10-31 | OK
x | LV Voltage, HV Side after D11 | U_in = 0 V / DC/DC Enabled, IDLE, 12.2 V LV | 11.79 | V |  |  | 2024-10-31 | OK
x | LV Voltage, HV Side after D14 | U_in = 0 V / DC/DC Enabled, IDLE, 12.2 V LV | 12.108 | V |  |  | 2024-10-31 | OK
 | MOSFET top supply Voltage (VDDA-VSSA) | U_in = 200 V / DC/DC Enabled, IDLE, Cap @ 3,75 V | 11.71 | V |  |  | 2024-11-28 | OK | WARNING: DO NOT MEASURE THIS WITHOUT EXTRA PRECAUTION! HV SWITCHNODE!
 | MOSFET top supply Voltage (VDDA-VSSA) | U_in = 300 V / DC/DC Enabled, IDLE, Cap @ 3,75 V | 11.82 | V |  |  | 2024-11-28 | OK | WARNING: DO NOT MEASURE THIS WITHOUT EXTRA PRECAUTION! HV SWITCHNODE!
 | MOSFET top supply Voltage (VDDA-VSSA) | U_in = 400 V / DC/DC Enabled, IDLE, Cap @ 3,75 V | 11.96 | V |  |  | 2024-11-28 | OK | WARNING: DO NOT MEASURE THIS WITHOUT EXTRA PRECAUTION! HV SWITCHNODE!
 | MOSFET top supply Voltage (VDDA-VSSA) | U_in = 500 V / DC/DC Enabled, IDLE, Cap @ 3,75 V | 11.40 | V |  |  | 2024-11-28 | OK | WARNING: DO NOT MEASURE THIS WITHOUT EXTRA PRECAUTION! HV SWITCHNODE!
 | MOSFET top supply Voltage (VDDA-VSSA) | U_in = 600 V / DC/DC Enabled, IDLE, Cap @ 3,75 V | 10.66 | V |  |  | 2024-11-28 | OK | WARNING: DO NOT MEASURE THIS WITHOUT EXTRA PRECAUTION! HV SWITCHNODE!
 | Precharge | Precharge Close delay | 5,0 ... 5,3 | ms |  |  | 2024-11-27 | OK | Only slightly dependent on U_in
 | Precharge | Precharge Close Voltage Jump | 9 | V |  |  | 2024-11-27 | OK | Hard to measure, simulation might be more accurate
 | Precharge | Precharge Open Delay | 7 | ms |  |  | 2024-11-28 | OK
 | Precharge | Mad-Scruti-Test (Enable/Disable DC/DC as mad as possible) | PASS |  |  |  | 2024-11-28 | OK
 | Precharge | Precharge Time 200 V to 60V, 21°C RT | 68 | ms |  |  | 2024-11-27 | OK
 | Precharge | Precharge Time 300 V to 60V, 21°C RT | 103 | ms |  |  | 2024-11-27 | OK
 | Precharge | Precharge Time 400 V to 60V, 21°C RT | 141 | ms |  |  | 2024-11-27 | OK
 | Precharge | Precharge Time 500 V to 60V, 21°C RT | 180 | ms |  |  | 2024-11-27 | OK
 | Precharge | Precharge Time 600 V to 60V, 21°C RT | 221 | ms |  |  | 2024-11-27 | OK
 | Passive Discharge | Discharge Time 200 V to 60V, 21°C RT | 1.592 | s |  |  | 2025-01-07 | OK
 | Passive Discharge | Discharge Time 300 V to 60V, 21°C RT | 2.120 | s |  |  | 2025-01-07 | OK
 | Passive Discharge | Discharge Time 400 V to 60V, 21°C RT | 2.540 | s |  |  | 2025-01-07 | OK
 | Passive Discharge | Discharge Time 500 V to 60V, 21°C RT | 2.795 | s |  |  | 2025-01-07 | OK
 | Passive Discharge | Discharge Time 600 V to 60V, 21°C RT | 3.045 | s |  |  | 2025-01-07 | OK
 | Leakage Current Turned off | 200 V, 21°C RT | 15 | nA |  |  | 2024-11-27 | OK | 13,3 GΩ
 | Leakage Current Turned off | 300 V, 21°C RT | 28 | nA |  |  | 2024-11-27 | OK | 10,7 GΩ
 | Leakage Current Turned off | 400 V, 21°C RT | 41 | nA |  |  | 2024-11-27 | OK | 9,8 GΩ
 | Leakage Current Turned off | 500 V, 21°C RT | 56 | nA |  |  | 2024-11-27 | OK | 8,9 GΩ
 | Leakage Current Turned off | 600 V, 21°C RT | 75 | nA |  |  | 2024-11-27 | OK | 8,0 GΩ
 | Input Current, Turned ON, below UVP | 50V, 21°C RT | 75 | µA |  |  | 2024-12-11 | OK
 | Input Current, Turned ON, below UVP | 100V, 21°C RT | 151 | µA |  |  | 2024-12-11 | OK
 | Input Current, Turned ON, below UVP | 150V, 21°C RT | 228 | µA |  |  | 2024-12-11 | OK
 | Input Current, Turned ON, below UVP | 200V, 21°C RT | 305 | µA |  |  | 2024-12-11 | OK
 | Input Current, Turned ON, above UVP | 200 V, 21°C RT, no Fan, dead time = 80° | 40.0 | mA | 8.00 | W | 2025-01-07 | OK
 | Input Current, Turned ON, above UVP | 300 V, 21°C RT, no Fan, dead time = 80° | 27.2 | mA | 8.16 | W | 2025-01-07 | OK
x | Input Current, Turned ON, above UVP | 400 V, 21°C RT, no Fan, dead time = 80° | 20.8 | mA | 8.32 | W | 2025-01-07 | OK
x | Input Current, Turned ON, above UVP | 500 V, 21°C RT, no Fan, dead time = 80° | 16.7 | mA | 8.33 | W | 2025-01-07 | OK
x | Input Current, Turned ON, above UVP | 600 V, 21°C RT, no Fan, dead time = 80° | 11.34 | mA | 6.80 | W | 2025-01-07 | OK
 | Oscillator | Soft Startup no C34 frequency | 190.6 | kHz |  |  | 2024-11-28 | OK | Calculated
 | Oscillator | Soft Startup no C34 lenght | 263 | ms |  |  | 2024-11-28 | OK | Calculated
x | Oscillator | Soft Startup with C34 = 22uF/1k frequency | 347 | kHz |  |  | 2024-11-28 | OK
 | Oscillator | Soft Startup with C34 = 22uF/1k lenght, f_sw 350 kHz to 94 kHz | 242 | ms |  |  | 2024-11-28 | OK
 | Oscillator | Dead time min. | 119 | ns |  |  | 2024-11-03 | OK
 | Oscillator | Dead time middle | 274 | ns |  |  | 2024-11-03 | OK
 | Oscillator | Dead time max. | 505 | ns |  |  | 2024-11-03 | OK
 | Oscillator | Dead time potentiometer dead-room | 60 | ° |  |  | 2024-11-03 | OK
 | Oscillator | Dead time, efficiency optimum 200 V | 80 | ° | 2,96 kΩ |  | 2025-01-07 | OK
 | Oscillator | Dead time, efficiency optimum 300 V | 80 | ° | 2,96 kΩ |  | 2025-01-07 | OK
 | Oscillator | Dead time, efficiency optimum 400 V | 80 | ° | 2,96 kΩ |  | 2025-01-07 | OK
 | Oscillator | Dead time, efficiency optimum 500 V | 80 | ° | 2,96 kΩ |  | 2025-01-07 | OK | optimum does not change at 100W load
 | Oscillator | Dead time, efficiency optimum 600 V | 80 | ° | 2,96 kΩ |  | 2025-01-07 | OK
 | Oscillator | frequency Potentiometer shipped | 40 | kHz |  |  | 2024-11-03 | OK
 | Oscillator | frequency min. | 20 | kHz |  |  | 2024-11-03 | OK
 | Oscillator | frequency max. | 330 | kHz |  |  | 2024-11-03 | OK
x | Oscillator | frequency min. recommended | 90 | kHz |  |  | 2024-11-03 | OK | 1,97 kΩ, but unsure what f_min is right now
 | Misc | Input reverse polarity Diode Test, 0.1A | -4.48 | V |  |  | 2024-11-28 | OK
 | Misc | Input reverse polarity Diode Test, 0.5A | -5.04 | V |  |  | 2024-11-28 | OK
 | Misc | Input reverse polarity Diode Test, 1A | -5.34 | V |  |  | 2024-11-28 | OK
 | Misc | Input reverse polarity Diode Test, 2A | -5.83 | V |  |  | 2024-11-28 | OK
 | Input | Input Voltage Ripple, 0A Load, 400V | 0.741 | Vrms |  |  | 2024-12-20 | OK | NO LISN, Direct PFC feed with SDM inbetween
 | Input | Input Voltage Ripple, 0A Load, 400V | 7.1 | Vpp |  |  | 2024-12-20 | OK but improveable | NO LISN, Direct PFC feed with SDM inbetween
 | Input | Input Voltage Ripple, 10A Load, 400V | 0.96 | Vrms |  |  | 2024-12-20 | OK | NO LISN, Direct PFC feed with SDM inbetween
 | Input | Input Voltage Ripple, 10A Load, 400V | 8.51 | Vpp |  |  | 2024-12-20 | OK but improveable | NO LISN, Direct PFC feed with SDM inbetween
 | Input | Input Voltage Ripple, 20A Load, 400V | 0.52 | Vrms |  |  | 2024-12-20 | OK | NO LISN, Direct PFC feed with SDM inbetween
 | Input | Input Voltage Ripple, 20A Load, 400V | 7.86 | Vpp |  |  | 2024-12-20 | OK but improveable | NO LISN, Direct PFC feed with SDM inbetween
 | Input | Input Voltage Ripple, 30A Load, 400V | 0.73 | Vrms |  |  | 2024-12-20 | OK | NO LISN, Direct PFC feed with SDM inbetween
 | Input | Input Voltage Ripple, 30A Load, 400V | 6.97 | Vpp |  |  | 2024-12-20 | OK but improveable | NO LISN, Direct PFC feed with SDM inbetween
 | Input | Input Voltage Ripple, 0A Load, 500V | 5.56 | Vpp |  |  | 2024-12-20 | OK but improveable | NO LISN, Direct PFC feed with SDM inbetween
 | Input | Input Voltage Ripple, 0A Load, 600V | 3.0 | Vpp |  |  | 2024-12-20 | OK but improveable | NO LISN, Direct PFC feed with SDM inbetween
 | Output | output Voltage Ripple, 0A Load, 400V | 5.1 | mVrms |  |  | 2024-12-08 | OK | T747, NO LISN, Direct Load feed
 | Output | output Voltage Ripple, 0A Load, 400V | 152 | mVpp |  |  | 2024-12-08 | OK | T747, NO LISN, Direct Load feed
 | Output | output Voltage Ripple, 10A Load, 400V | 9.1 | mVrms |  |  | 2024-12-08 | OK | T748, NO LISN, Direct Load feed
 | Output | output Voltage Ripple, 10A Load, 400V | 189 | mVpp |  |  | 2024-12-08 | OK | T748, NO LISN, Direct Load feed
 | Output | output Voltage Ripple, 20A Load, 400V | 13.2 | mVrms |  |  | 2024-12-08 | OK | T749, NO LISN, Direct Load feed
 | Output | output Voltage Ripple, 20A Load, 400V | 230 | mVpp |  |  | 2024-12-08 | OK | T749, NO LISN, Direct Load feed
 | Output | output Voltage Ripple, 30A Load, 400V | 18.9 | mVrms |  |  | 2024-12-08 | OK | T750, NO LISN, Direct Load feed
 | Output | output Voltage Ripple, 30A Load, 400V | 310 | mVpp |  |  | 2024-12-08 | OK | T750, NO LISN, Direct Load feed
x | Voltage Regulation | output Voltage, 25°C RT | 24,09 ... 24,16 | V |  |  | 2024-11-27 | OK | depends on converter temperature
x | Voltage Regulation | minimum HV input for 24 V Output, set by f_min = 94 kHz | 180 | V |  |  | 2024-11-27 | OK
 | Voltage Regulation | Overshoot test with 4700 uF Load (uncharged), 400 V | 1.7 | Vp | 162 ms |  | 2024-12-08 | OK but improveable
 | Voltage Regulation | Overshoot test with 4700 uF Load (uncharged), 500 V | 0.83 | Vp | 118 ms |  | 2024-12-08 | OK
 | Voltage Regulation | Overshoot test with 4700 uF Load (uncharged), 600 V | 0.34 | Vp | 36 ms |  | 2024-12-08 | OK
 | Voltage Regulation | Undershoot test with 300W Load 400 V | 38 | mVp | 40 ms down / 1,8 up? |  | 2024-12-08 | OK
 | Voltage Regulation | Undershoot test with 300W Load 500 V | 38 | mVp | 46 ms down / 1,3s Up? |  | 2024-12-08 | OK
 | Voltage Regulation | Undershoot test with 300W Load 600 V | 43 | mVp | 52 ms down / 1,8 s up? |  | 2024-12-08 | OK
x | UVP | lock-in, 1.7 MΩ | 199 | V |  |  | 2024-11-27 | OK
x | UVP | lock-out, 1.7 MΩ | 206 | V |  |  | 2024-11-27 | OK
 | UVP | lock-in delay, 1.7 MΩ, C47 = 22nF, 200V | 234 | ms |  |  | 2024-11-27 | OK
 | UVP | lock-in delay, 1.7 MΩ, C47 = 22nF, 300V | 52 | ms |  |  | 2024-11-27 | OK
 | UVP | lock-in delay, 1.7 MΩ, C47 = 22nF, 400V | 28 | ms |  |  | 2024-11-27 | OK
 | UVP | lock-in delay, 1.7 MΩ, C47 = 22nF, 500V | 19 | ms |  |  | 2024-11-27 | OK
 | UVP | lock-in delay, 1.7 MΩ, C47 = 22nF, 600V | 14 | ms |  |  | 2024-11-27 | OK
x | OVP | lock-in, 543 kΩ | 609 | V |  |  | 2024-11-28 | OK
x | OVP | lock-out, 543 kΩ | 598 | V |  |  | 2024-11-28 | OK
 | UCC25600 Overcurrent Protection | Voltage mesured over C_res = 22,4 nF, U_in = 200 V | 290 | V |  |  | 2024-11-27 | tested but inaccurate, not important
x | Overtemperature Lock-out | TL072, 330k || 4k7, C28 = 100nF, C48 = 10nF | 106.9 | °C |  |  | 2024-11-15 | OK
x | Overtemperature Lock-in | TL072, 330k || 4k7, C28 = 100nF, C48 = 10nF | 104 | °C |  |  | 2024-11-15 | OK
x | Fan control turn-on | TL072 | 71 | °C |  |  | 2024-11-28 | OK
x | Fan control turn-off | TL072 | 61 | °C |  |  | 2024-11-28 | OK
x | Fan control Sensor Loss | Fan behavior | always on |  |  |  | 2024-11-28 | OK
 | Fan 5V option | current @ 3,75 V | 150 | mA |  |  | 2024-12-08 | OK
 | Fan 5V option | 24V loop constrol influence | none |  |  |  | 2024-11-28 | OK
 | Fan 12V option | 24V loop constrol influence | none |  |  |  | 2024-11-28 | OK
 | Temperature | Temperature after 10 min, open Air, 5V Fan ON, 0A load, 500V | 53.4 | °C | 21°C RT |  | 2024-12-08 | OK
 | Temperature | Temperature after 10 min, open Air, 5V Fan ON, 10A load, 500V | 65.5 | °C | 21°C RT |  | 2024-12-08 | OK
 | Temperature | Temperature after 10 min, open Air, 5V Fan ON, 20A load, 500V | 77.6 | °C | 21°C RT |  | 2024-12-08 | OK
 | Temperature | Temperature after 5 min, open Air, 5V Fan ON, 25A load, 500V | 101.7 | °C | 21°C RT |  | 2024-12-08 | OK
 | Temperature | Temperature after 10 min, open Air, 5V Fan ON, 25A load, 500V | 102.9 | °C | 21°C RT |  | 2024-12-08 | OK
 | Temperature | Temperature after 1 min, open Air, 5V Fan ON, 30A load, 500V | 102 | °C | 21°C RT |  | 2024-12-08 | OK
x | Hotbox Test, SR Temperature after 30 min | converter inside a box with rising temp, Air Temperaure max. 60°C must be able to deliver 500W at 500V at 60°C for 30 minutes and then be able to be restarted after 5 seconds | 104.7 | °C | 114.5 | °C | 2024-12-20 | OK | Sensor Temp / SR FET Temp
 | Turns Ratio | W1, W2, W3 | 28 : 2 : 2 |  |  |  | 2024-11-07 | OK
 | Litz Wire Lenght W1 (SN: 67) | Type: 120x 0.1 mm ø 0.92 mm^2 1.4 mm | 1780 | mm |  |  | 2024-11-07 | OK
 | Litz Wire Lenght W2 (SN: 68) | Type: 600x 0,071 mm ø 2,38 mm^2 2,4 mm | 185 | mm |  |  | 2024-11-07 | OK
 | Litz Wire Lenght W3 (SN: 69) | Type: 600x 0,071 mm ø 2,38 mm^2 2,4 mm | 165 | mm |  |  | 2024-11-07 | OK
x | Inductance W1 | 100 kHz 4 Vpp sine, N27+N97 | 166.3 | µH |  |  | 2024-11-07 | OK
x | Leakage Inductance W1 | W2 short, 100 kHz 4 Vpp Sine, AD2 = 10 Ω, N27+N97 | 56.32 | µH |  |  | 2024-11-07 | OK
x | Leakage Inductance W1 | W3 short, 100 kHz 4 Vpp Sine, AD2 = 10 Ω, N27+N97 | 56.11 | µH |  |  | 2024-11-07 | OK
 | Leakage Inductance W1 | W2 and W3 short, 100 kHz 4 Vpp Sine, AD2 = 10 Ω, N27+N97 | 53.85 | µH |  |  | 2024-11-07 | OK
x | Inductance W2 | 100 kHz 4 Vpp Sine, AD2 = 10 Ω, N27+N97 | 1.057 | µH |  |  | 2024-11-07 | OK
x | Inductance W3 | 100 kHz 4 Vpp Sine, AD2 = 10 Ω, N27+N97 | 1.014 | µH |  |  | 2024-11-07 | OK
x | Leakage Inductance W2 | 100 kHz 4 Vpp Sine, AD2 = 10 Ω, N27+N97 | 0.3557 | µH |  |  | 2024-11-07 | OK
x | Leakage Inductance W3 | 100 kHz 4 Vpp Sine, AD2 = 10 Ω, N27+N97 | 0.3496 | µH |  |  | 2024-11-07 | OK
 | Resistance W1 | DC, 20°C, 32,895 mV, 1008 mA | 32.63 | mΩ |  |  | 2024-11-07 | OK
 | Resistance W1 | DC, 100°C, 445,4 mV, 10504 mA, 21°C RT | 42.40 | mΩ |  |  | 2024-11-07 | OK | Temperarure coefficient (measured) | 0.38%
 | Resistance W1 | 10 kHz 4 Vpp sine, AD2 = 10 Ω, 2+3 shorted, 20°C | 140.2 | mΩ |  |  | 2024-11-07 | OK
 | Resistance W1 | 100 kHz 4 Vpp Sine, AD2 = 10 Ω, 2+3 shorted, 20°C | 145.4 | mΩ |  |  | 2024-11-07 | OK
 | Resistance W1 | 200 kHz 4 Vpp Sine, AD2 = 10 Ω, 2+3 shorted, 20°C | 552.6 | mΩ |  |  | 2024-11-07 | OK
 | Resistance W1 | 350 kHz 4 Vpp Sine, AD2 = 10 Ω, 2+3 shorted, 20°C | 1081 | mΩ |  |  | 2024-11-07 | OK
 | Resistance W1 | 1000 kHz 4 Vpp Sine, AD2 = 10 Ω, 2+3 shorted, 20°C | 14540 | mΩ |  |  | 2024-11-07 | OK
 | Resistance W2 | DC, 21°C, 6,740 mV, 5012 mA | 1.345 | mΩ |  |  | 2024-11-07 | OK
 | Resistance W2 | DC, 57°C, 30,46 mV, 19990 mA, 21°C RT | 1.524 | mΩ |  |  | 2024-11-07 | OK | Temperarure coefficient (measured) | 0.37%
 | Resistance W2 | 10 kHz 4 Vpp Sine, AD2 = 10 Ω, W1 shorted, 20°C | 2.4 | mΩ |  |  | 2024-11-07 | tested but inaccurate, not important
 | Resistance W2 | 100 kHz 4 Vpp Sine, AD2 = 10 Ω, W1 shorted, 20°C | 15.1 | mΩ |  |  | 2024-11-07 | tested but inaccurate, not important
 | Resistance W2 | 200 kHz 4 Vpp Sine, AD2 = 10 Ω, W1 shorted, 20°C | 6.2 | mΩ |  |  | 2024-11-07 | tested but inaccurate, not important
 | Resistance W2 | 350 kHz 4 Vpp Sine, AD2 = 10 Ω, W1 shorted, 20°C | 16.7 | mΩ |  |  | 2024-11-07 | tested but inaccurate, not important
 | Resistance W2 | 1000 kHz 4 Vpp Sine, AD2 = 10 Ω, W1 shorted, 20°C | 100.8 | mΩ |  |  | 2024-11-07 | OK
 | Resistance W3 | DC, 21°C, 5,884 mV, 5010 mA | 1.174 | mΩ |  |  | 2024-11-07 | OK
 | Resistance W3 | DC, 66°C 27,175 mV, 19986 mA, 21°C RT | 1.360 | mΩ |  |  | 2024-11-07 | OK | Temperarure coefficient (measured) | 0.35%
 | Resistance W3 | 10 kHz 4 Vpp Sine, AD2 = 10 Ω, W1 shorted | 2.4 | mΩ |  |  | 2024-11-07 | tested but inaccurate, not important
 | Resistance W3 | 100 kHz 4 Vpp Sine, AD2 = 10 Ω, W1 shorted | 18.3 | mΩ |  |  | 2024-11-07 | tested but inaccurate, not important
 | Resistance W3 | 200 kHz 4 Vpp Sine, AD2 = 10 Ω, W1 shorted | 13.7 | mΩ |  |  | 2024-11-07 | tested but inaccurate, not important
 | Resistance W3 | 350 kHz 4 Vpp Sine, AD2 = 10 Ω, W1 shorted | 3.5 | mΩ |  |  | 2024-11-07 | tested but inaccurate, not important
 | Resistance W3 | 1000 kHz 4 Vpp Sine, AD2 = 10 Ω, W1 shorted | 94.3 | mΩ |  |  | 2024-11-07 | OK
 | Saturation Current W1 | DC, 21°C RT | 7.9 | A |  |  | 2024-11-07 | OK
 | Winding Capacitance W1 || W2 | 4 Vpp, 1000 kHz, AD2 = 10 kΩ | 6.1 | pF |  |  | 2024-11-07 | OK
 | Winding Capacitance W1 || W3 | 4 Vpp, 1000 kHz, AD2 = 10 kΩ | 5.9 | pF |  |  | 2024-11-07 | OK
 | Winding Capacitance W1 || W2+W3 | 4 Vpp, 1000 kHz, AD2 = 10 kΩ | 6.9 | pF |  |  | 2024-11-07 | OK
 | Winding Capacitance W2 || W3 | 4 Vpp, 1000 kHz, AD2 = 10 kΩ | 26.3 | pF |  |  | 2024-11-07 | OK
 | Resonant Frequ. W1 | 4 Vpp, AD2 = 100 Ω | 8.0 | MHz |  |  | 2024-11-07 | OK
 | Typ. Frequency Range | 0 W Load, U_in = 200 ... 600 V | 95 ... 200 | kHz |  |  | 2024-11-17 | OK
 | Typ. Frequency Range | 250 W Load, U_in = 200 ... 600 V | 90 ... 170 | kHz |  |  | 2024-11-17 | OK
 | Typ. Frequency Range | 750 W Load, U_in = 400 ... 600 V | 115 ... 160 | kHz |  |  | 2024-11-17 | OK
 | Typ. Input Voltage W1 | Resonant Half Bridge | 300 | V |  |  | 2024-11-17 | OK
 | Typ. Output Voltage W2, W3 | Resonant Half Bridge | 24.0 | V |  |  | 2024-11-17 | OK
 | Typ. LLC Gain | Resonant Half Bridge | 1,1 ... 3,4 |  |  |  | 2024-11-17 | OK
 | Isolation | 1 minute DC, no Isolation breakdown | 5000 | V RMS |  |  | 2024-11-06 | OK
 | Isolation | Isolation Resistance (DC) | ≥ 200 | GΩ |  |  | 2024-11-06 | OK
x | Isolation | 1 minute AC, 50 Hz, no Isolation breakdown | 3000 | V RMS |  |  | 2024-11-06 | OK
 | Typ. Current W1 | 0 W conversion Power, U_in = 200 ... 600 V | 1,6 ... 2,8 | A RMS |  |  | 2024-11-17 | OK
 | Typ. Current W1 | 250 W conversion Power, U_in = 200 ... 600 V | 2,4 ... 3,6 | A RMS |  |  | 2024-11-17 | OK
 | Typ. Current W1 | 750 W conversion Power, U_in = 400 ... 600 V | 4,2 ... 4,8 | A RMS |  |  | 2024-11-17 | OK
 | Typ. Current W2 + W3 | 750 W, W2 + W3 combined current, equal load share | 31.5 | A RMS |  |  | 2024-11-27 | OK
 | Coil Former Temp. Rating | Material: Liqcreate Flame Retardant HDT | 250 | °C |  |  | - | OK
 | Coil Former FR Level | Material: Liqcreate Flame Retardant HDT | UL94 V-0 |  |  |  | - | OK
 | Winding Temp. Rating | Primary and Secondary Windings | 155 | °C |  |  | - | OK
 | Core | Material | N27 + N97 |  |  |  | - | OK
 | typ. Core Temperature | TDK SIFERRIT N97, ETD39 | 80 ... 120 | °C |  |  | 2024-11-17 | OK
 | Core Saturation Flux density | 100°C, TDK SIFERRIT N97, ETD39 | 410 | mT |  |  | - | OK
 | Core Relative Losses | 100 kHz, 200 mT, TDK SIFERRIT N97, ETD39 | 0.30 | W/cm³ |  |  | - | OK
 | Core Air Gap | total Air Gap length between both cores | 1000 | µm |  |  | - | OK
 | Transformer Power Dissipation W1 | Passive Convection, DC, 445,4 mV, 10504 mA Hotspot ≤ 100°C unlimited time, RT 21°C | 4.7 | W |  |  | 2024-11-07 | OK
 |  | Active Convection, DC, 603,9 mV, 13998 mA Fan: 0.5 W @ 3,75V 30 x 30 x 7 mm, 5 m³/h, Manufacturer: UltraFan, Type: XD3007D5H, 5V, 200 mA, Top Cooled Hotspot ≤ 100°C unlimited time, 21°C RT, | 8.5 | W |  |  | 2024-11-07 | OK
 | Transformer Power Dissipation W2 | Passive Convection, DC, 30,46 mV, 19990 mA Hotspot = 57°C, unlimited time, 21°C RT | 0.61 | W |  |  | 2024-11-07 | OK
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

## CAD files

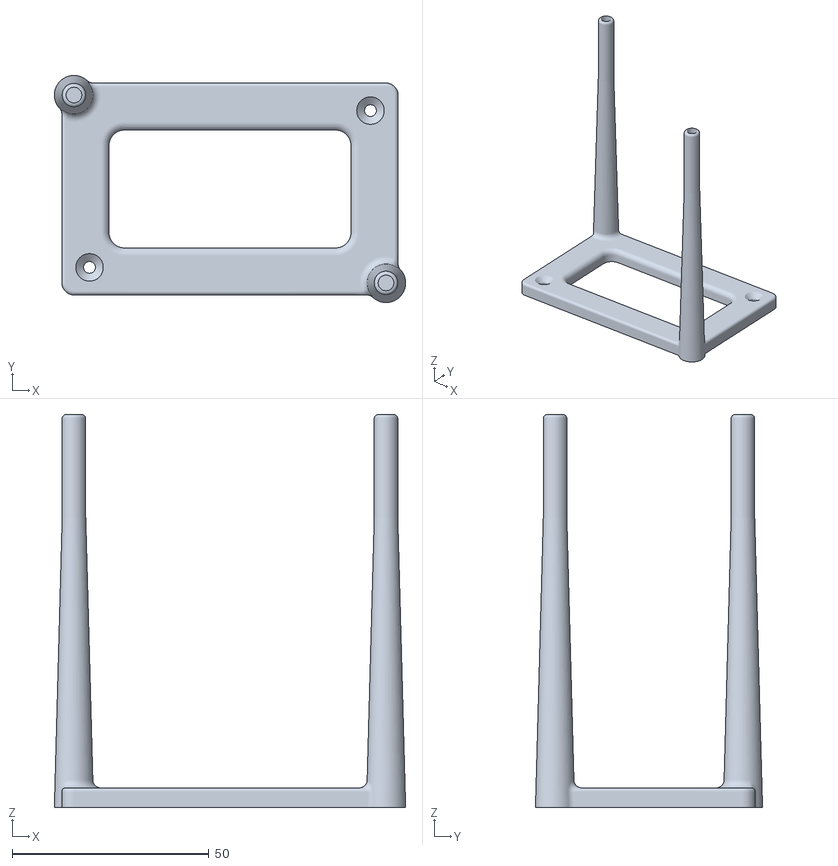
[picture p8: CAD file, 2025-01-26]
extra/DCDCv9_test_mount.stl
89.4 x 57.8 x 100.0

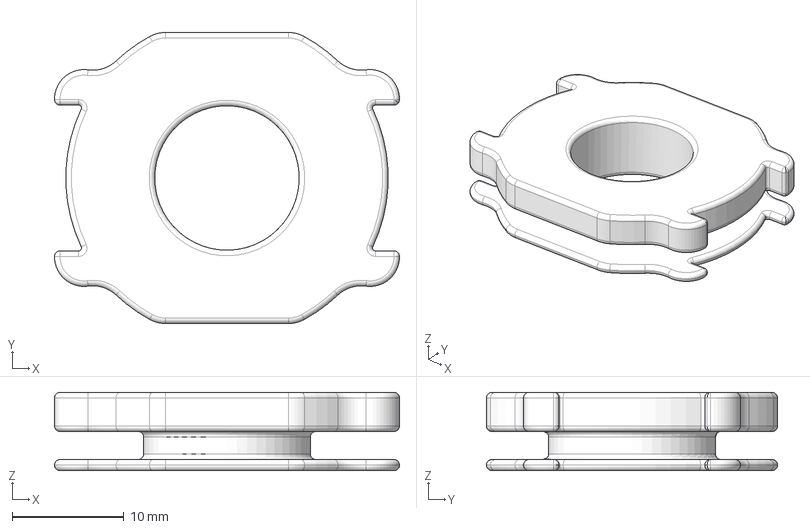
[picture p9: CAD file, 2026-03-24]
transformer/ETD39_sek_single_winding.step
30.8 x 26.0 x 7.00 mm

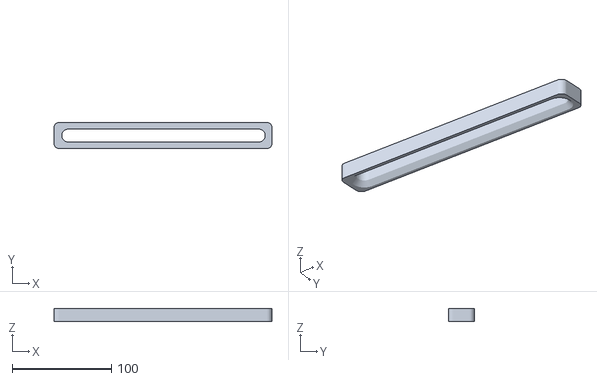
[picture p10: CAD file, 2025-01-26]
transformer/grinding holder/ETD39_core_slider_guide.stl
220.0 x 26.4 x 13.0

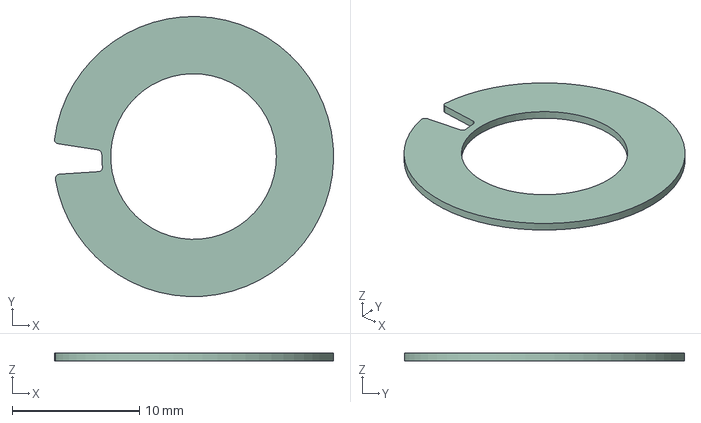
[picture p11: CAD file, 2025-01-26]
transformer/pcb-transformer-test/pcb-isolator/pcb-isolator.step
21.9 x 22.0 x 0.6 mm

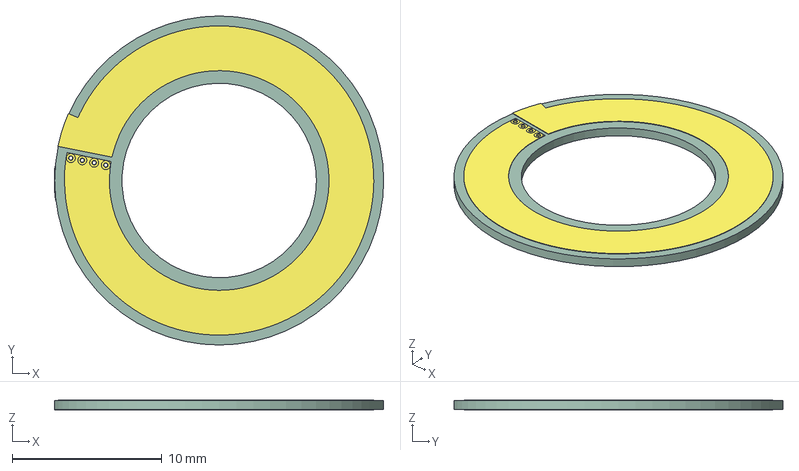
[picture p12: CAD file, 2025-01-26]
transformer/pcb-transformer-test/pcb-winding/pcb-winding.step
22.0 x 22.0 x 0.67 mm
_autosave-pcb-transformer_track_1
_autosave-pcb-transformer_track_2
_autosave-pcb-transformer_pad_1
_autosave-pcb-transformer_pad_2
_autosave-pcb-transformer_pad_3
_autosave-pcb-transformer_pad_4
_autosave-pcb-transformer_pad_5
_autosave-pcb-transformer_pad_6
_autosave-pcb-transformer_pad_7
_autosave-pcb-transformer_pad_8
_autosave-pcb-transformer_pad_9
_autosave-pcb-transformer_pad_10
_autosave-pcb-transformer_pad_11
_autosave-pcb-transformer_pad_12
_autosave-pcb-transformer_pad_13
_autosave-pcb-transformer_pad_14
_autosave-pcb-transformer_pad_15
_autosave-pcb-transformer_PCB

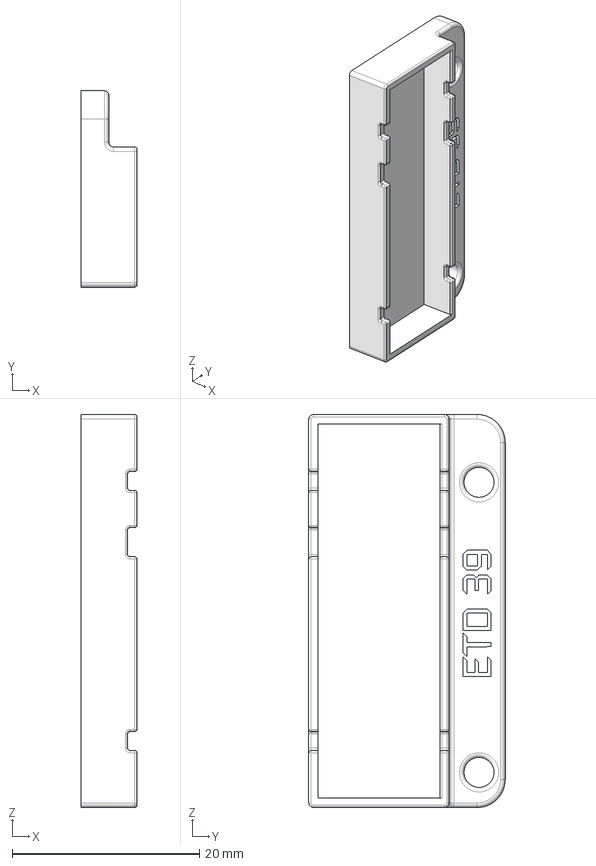
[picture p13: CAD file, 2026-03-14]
transformer/ETD39_transformer_isolator.step
6.00 x 21.0 x 42.0 mm

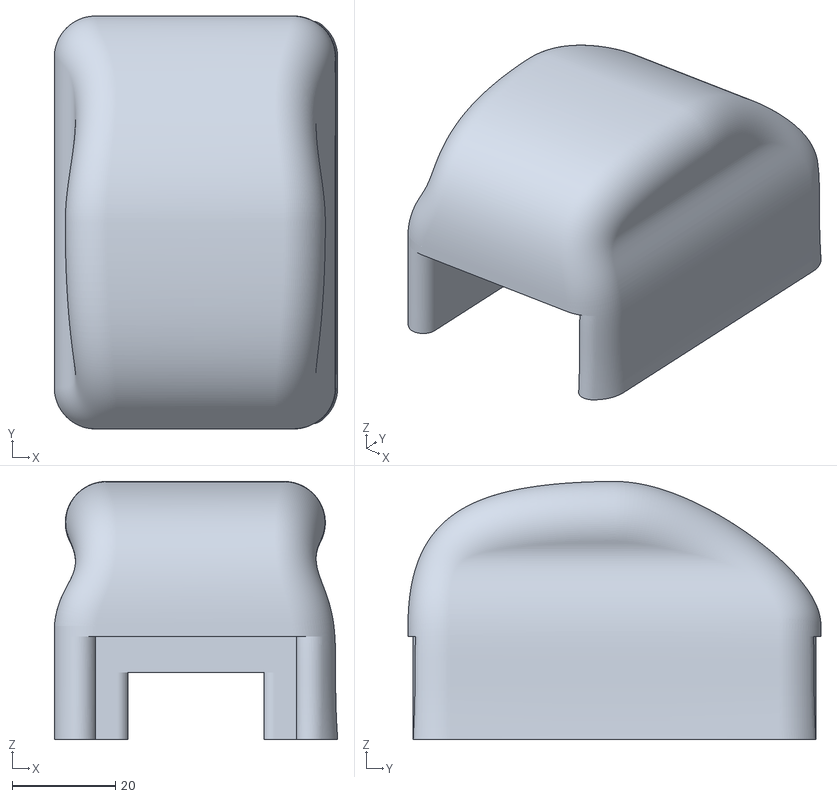
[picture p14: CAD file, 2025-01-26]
transformer/grinding holder/ETD39_grinding_holder.stl
54.9 x 80.0 x 50.0

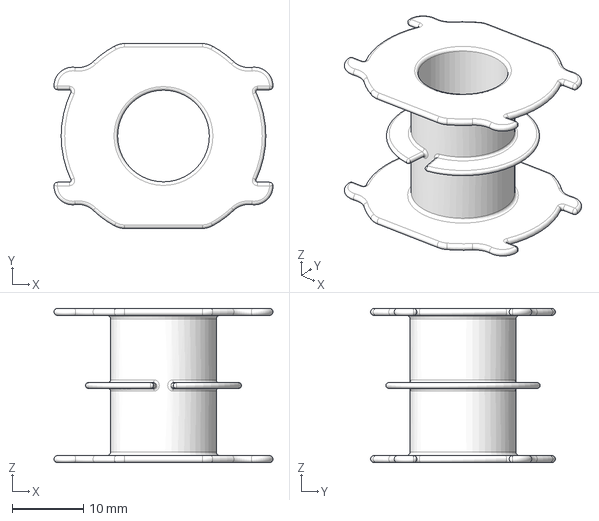
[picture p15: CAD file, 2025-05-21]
transformer/ETD39_prim.step
30.8 x 26.0 x 21.7 mm

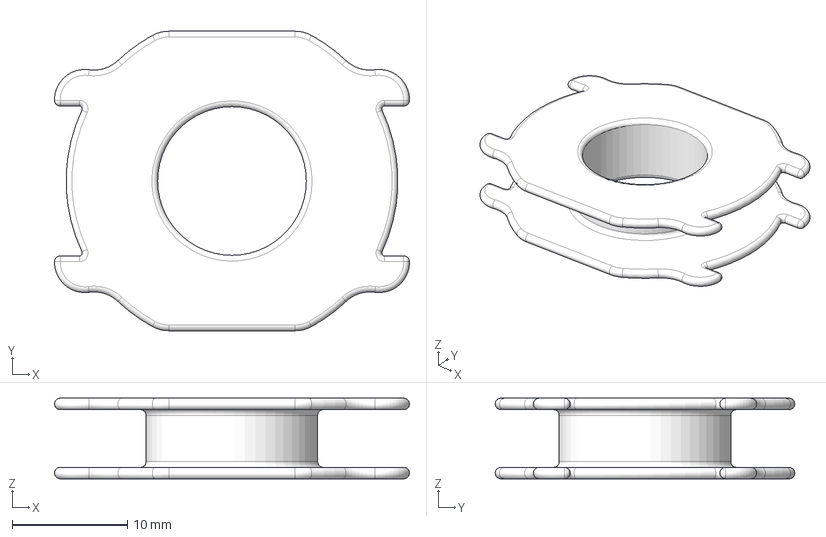
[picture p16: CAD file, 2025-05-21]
transformer/ETD39_sek.step
30.8 x 26.0 x 7.00 mm

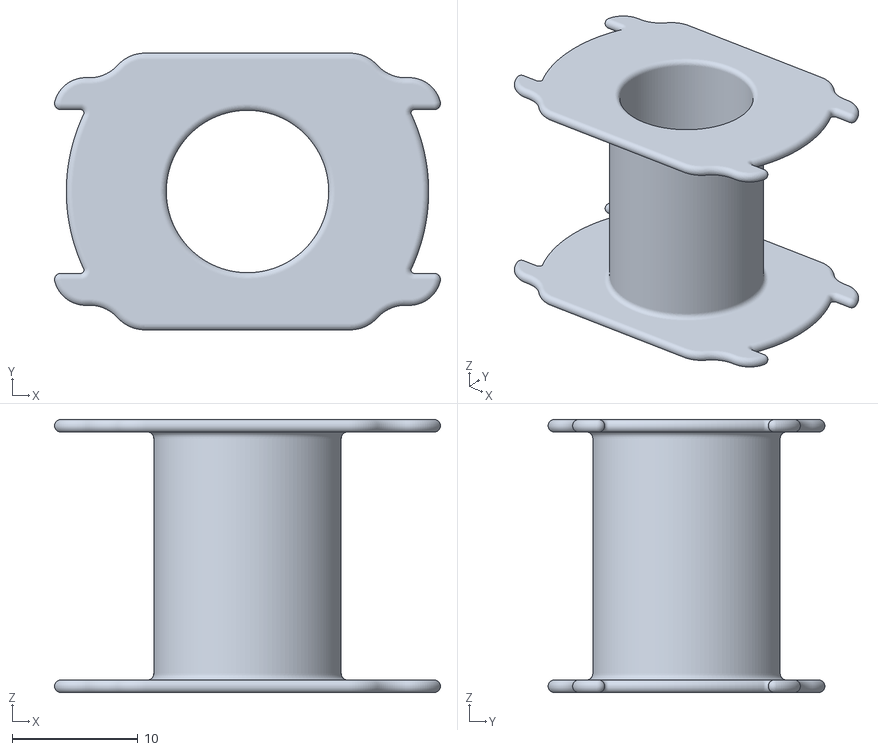
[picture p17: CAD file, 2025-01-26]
transformer/ETD39_prim_plain.stl
30.7 x 22.0 x 21.7

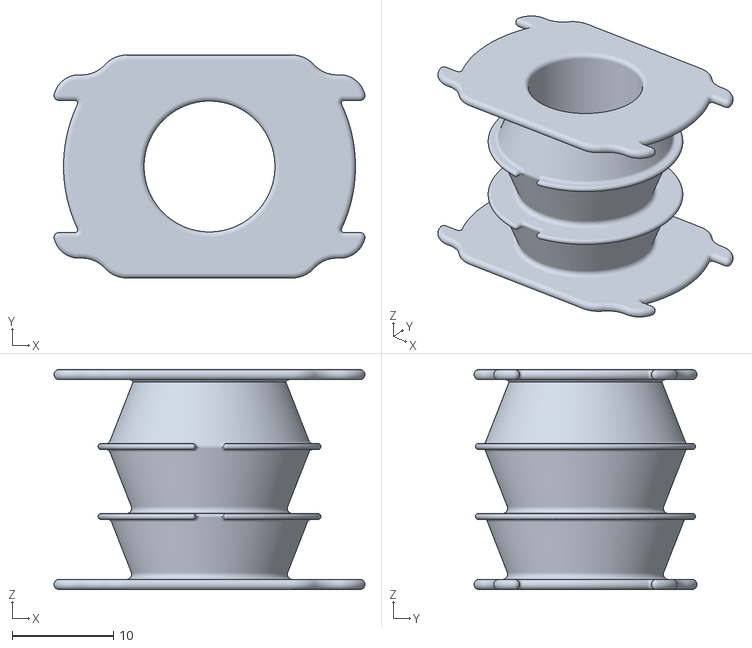
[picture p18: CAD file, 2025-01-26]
transformer/ETD39_prim_Bank-winding.stl
30.7 x 22.0 x 21.7

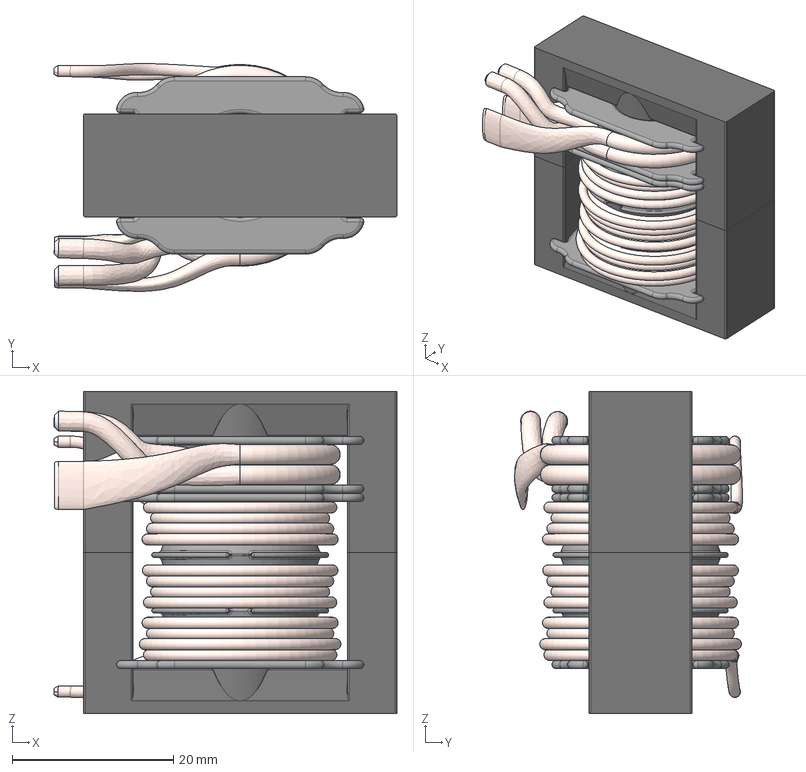
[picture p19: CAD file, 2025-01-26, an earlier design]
transformer/ETD39_complete_Transformer v9-3_old.step
42.5 x 28.3 x 40.0 mm

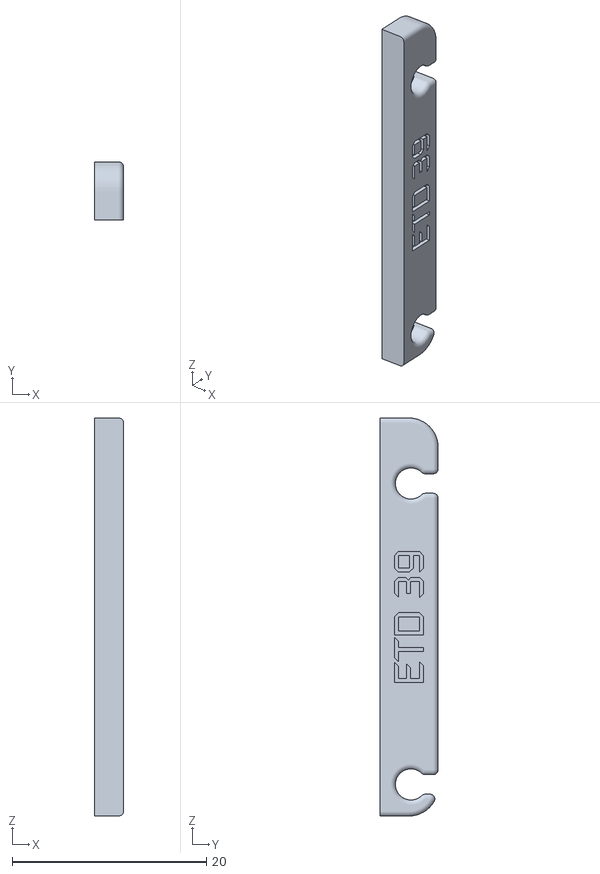
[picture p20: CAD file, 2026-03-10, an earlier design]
transformer/ETD39_addition_for_old_isolator.stl
3.00 x 6.00 x 41.0

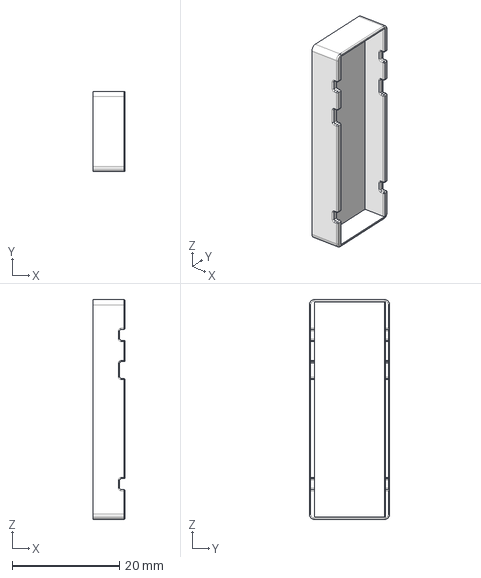
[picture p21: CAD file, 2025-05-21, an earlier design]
transformer/ETD39_transformer_isolator_old.step
6.00 x 15.0 x 41.0 mm

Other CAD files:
transformer/ETD39_prim.stl
transformer/ETD39_sek.stl
transformer/ETD39_sek_single_winding.stl
transformer/ETD39_transformer_isolator.stl
transformer/ETD39_transformer_isolator_old.stl

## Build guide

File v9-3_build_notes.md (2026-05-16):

# Build Notes v9-3

Hi there! 
Over the last months I've received countless questions and issues related to building a v9-3 replica. 
In this document I'll try to address them _cleanly_, so you don't have to dig trough the forum discussions, which unfortunately has gotten somewhat convoluted.

_Please note that I'm using YYMMDD, because I'm sick of other date formats. Old topics go last._

|Date | Title | Description |
|:---:|:---|:---|
|260516| MP4541 not available| The MP4541 seems to be not in stock on multiple sites. The [MP4581](https://www.mouser.de/ProductDetail/Monolithic-Power-Systems-MPS/MP4581GN-P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) can be used instead, it's the 100V-variant and 1:1 compatible.
|260511| U1 wrong part number| I falsely updated U1 in the DCDCv9-3r1.4 release as RP-1515S (15V version). The correct part number is RP-1212S (12V version). I'm sorry! Note to affected users: It might be, that the converter works with the RP-1515S version, as the output voltage is roughly equal to the input voltage. However, the 15V version might deliver less max. current at 12V, which could lead to failure at higher loads/voltage. Please exchange the component for the 12V version.|
|260410| R1, R71 wrong JLC part number| Although the issue first described in 260208 was due to a wrong assignment from JLC, I forgot to update the corresponding JLC part number, so PCBAs until now might be shipped with R1, R71 being 100 mOhm instead of 100 MOhm. I'm sorry for the inconvenience! Thanks to @a03254 for reporting this!
|260324| Wrong U7 pinout version in PCBA BOM | The TL431 referenced in the Kicad files is correct (TL431BCDBZR). However, in the BOM for the PCBA the LCSC part number was wrong (C963380). The correct part number is C6971. This has been fixed with the latest commit. Sorry for the inconvenience - I don't know how that happened, because on my only PCBA order it is correctly C6971. Background: For some unkown reasons, some companies are selling a mirrored pin version. E.g. Nexperia is selling these with "MFDT" in the Mfr. Number. The correct pin assigment for the SOT-23 Package is: 1 - Cathode, 2 - Reference, 3 - Anode. The thing is: The TL431 with swapped Cathode/Reference is equal to the TL432 - there is no other change than than the pin-out. Great. If your converter happen to output a gate signal only shortly at start-up then the wrong U7 can be the issue.|
|260314| Resolved EV 4.5.15 among others issues | An adhesive has been tested suitable to mechanically secure devices against loosening even at temperatures above 300°C with good reworkability. Furthermore, a new isolator design is released to secure the transformer litz to the PCB. Replicas with the isolator part before the 260314 changes can use a additional 3D-Printed part to comply. The HV input connector has been replaced with a Molex 43650-0315 as the previous terminal block did not provide a positive locking. Replicas using the input connector prior to the 260314 changes can use the Würth 691416600002 push-in terminal block, which utilises the same footprint. However, it exposes TS potential when connecting or removing the individual (live) wires. Therefore, another cable-mounted connector is recommended to safely (un)install the converter. All necessary changes have been implemented to all relevant documents and files with the release DCDCv9-3r1.4. Teams who have built their replica prior to this release should re-read the build guide on the pages stated in the revision history (last page).|
|260310| Primary Windings| In previous versions of all documents, it was incorrectly stated that the primary had 28 windings. The actual number used in the v9-3 was 29 windings. If your primary inductance is 153 ± 5 µH, it is likely that there are 28 windings. At 166 ± 5 µH there are likely 29 windings. Using 29 windings results in around 3 % lower currents and around 6 % lower switching speeds compared to 28 windings. However, due to the complexity of calculating HF transformer losses, changes in losses can only be determined with certainty through measurements taken during actual operation. In any case, simulations show that both configurations are suitable, due to their small differences. I would be interested to hear from anyone who has tested the version with 28 windings regarding their efficiency and transformer temperatures - please contact me on Reddit or Discord.|
|260308| Resolving EV 4.5.15| In September 2025, the issue regarding soldering in the high current path was brought up (see issue #10 ). One of the main points was that the high frequency litz could be considered as "wire" and thus not allowed in respect of EV 4.5.15 "the connected devices are not cells or wires". Thanks to a rules question by another team, we received the following response: `"In your case, the transformer should not be considered a soldered wire on a PCB, so it is not in conflict with EV 4.5.15."` Now the only point in EV 4.5.15 remaining open is "the devices are additionally mechanically secured against loosening". The solution has been inplemented in the 260314 update. |
|260220| Replicant induced layout changes | If you are running into issues while testing when using a modified design, please doublecheck all layout changes by comparing it with my original ones (open with KiCad 8.0.9 or compare the gerber files). The v9-3 design was created using KiCad 8.0.9 . I do not recommend for this design using KiCad 9 or later, as some features may be handled differently (e.g. custom rules). In case of issues while testing, please provide your KiCad files anlong the message. Note: I do not accept Altium Files. In this case please provide gerber files.|
|260208|PCBA resistors replaced with milli Ohm instead of mega Ohm| When ordering the PCB with assembled parts (PCBA), the high voltage resistors R1 and R71 in the 2512 package might be not on stock at JLC and therefore repleaced with others with 100 mOhm instead of 100 MOhm. There should be a warning on those components being replaced at the PCBA component selection. Either choose matching resistors (similar Voltage rating, same Resistance and package) or do not place them for PCBA and order at e.g. Mouser instead. A symptom of this is the precharge LED lighting up at initial tests with low voltage at the HV input above around 15V to 20V. If this goes unnoticed at higher HV input voltages, breaking U14 might be possible. However, as the precharge is only precharging in this state, the max. input current is limited to 5.5 mA 😄|
|260100|Measuring Lp and Lr correctly|To measure those values, you don't need an expensive Analog discovery. A cheap LCR-Meter works well enough in most cases (I've done so for years before I got the AD2). The donwnside is, that cheap LCR meters might measure based on resonant frequency, which depends on inductance. If it is measured at 350 kHz expect around 1% of increase of inductance from my measurements at 100 kHz. Measurements down to 10 kHz usually do not differ much from those at 100 kHz. If you're measuring Lr, make sure to short only one of the secondary coils. Use a alligator clip to directly short / press both ends of a secondary together - DO NOT use a cable inbetween both ends, as the length of the cable (even a few centimeters) will increase the inductance value significantly! Also keep the cables from the LCR Meter very short and apply open-short compensation.|
||||
<br>

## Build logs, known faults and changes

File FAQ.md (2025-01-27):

# <span style="color:green">Q&A</span>

Q: &ensp;How long does it take to build and test a DCDC?<br>
A: &ensp; If you are really nuts, you can do it as a single person in one day (but I don't recommend this). There are currently 190 components on the board, which can be soldered in 2 - 3 hours with good preparation and experience using solder paste (without stecil) and hot air. The longest time is needed to find and assign the correct components to the footprints. A board preassembled by JLC PCB (SMD only) may already contain approx. 80% of the components. This means that only about an hour is needed for the remaining components. The coil formers for the transformer require 2-4 hours depending on the SLA printer. Winding takes approx. 1 hour. Grinding and gluing the ETD cores takes approx. 30 minutes. Cleaning and drying of circuit boards, cores, SLA prints: total approx. 1 hour.<br>
If you want to build it properly, plan 1-2 days for building it, and 1-2 Weeks for lab testing before installing it.

Q: &ensp; Can I buy a whole converter from you?<br>
A: &ensp; Currently no. Assembling and testing it in a proper way would be so much work that (depending on demand) I couldn't do anything else. The cost of the effort would be many times higher than the material value of the converter, and the DIY idea is somewhat lost. The legal responsibility in the event of problems or errors is also difficult. All tests of a converter up to completion are carried out to the best of my knowledge, but are not recognised or certified. However, it might be possible to obtain partially assembled boards and UL94 V-0 coil formers for further assembly from me.<br>
_Are you interested in making a larger production of the converter? Feel free to contact me via Reddit!_<br>

Q:	&ensp;HELP! QUICK!!!!1! DCDC broke!<br>
A:	&ensp;Well, that's you turn to learn ;)<br>
Please open a new issue. I will deliberately be slow in answering urgent questions, as there was enough time available with good planning - so at least try not to make it look urgent.
Provide as much information as possible (e.g. how long the converter has been turned on, ambient temperatures, input voltage, output load, ...) and add pictures if relevant.
I will try to help to the best of my availability, but as this is not my job, I cannot guarantee anything.

Q: 	&ensp;I need [insert voltage here], can I do that?<br>
A: 	&ensp;You could change the feedback voltage divider for small adjustments (+-2V or so from 24V).<br>
But if you need 12 V .. 48 V you should alter the number of secondary windings, otherwise you will get in trouble with the resonant design.<br>
Note, that the output capacitors and SR-FETs must be altered accordingly!
	
Q: 	&ensp;I need more Power!<br>
A: 	&ensp;Currently the design is limited by thermals. Adding a strong Fan would allow to draw 750 W continously.<br> 
More than 750 W would exhaust the resonant cicuit, requiring different C_res and L_m/L_r.<br> 
I was able to pull 1500 W from an older Version with a lent source/sink which was able to handle that much. <br> 
But currently I do not own such a powerful source/sink to conduct test in this area.<br>

Q: 	&ensp;Where do I get a cheap high voltage source for low power testing?<br>
A: 	&ensp;I have been using one for 10€ from amazon for many years, which can generate up to 
800 V (when both -+400 V rails are used) from a 8 to 32 V source (15 V input delivers most HV power, 25 W max.).
If you want to support me, you can use my affiliate link where I get a small commission 
when a purchase is made: https://amzn.to/3TRJJif<br>
In the docs there is an additional folder 'HV Source' for a 3D-printed case which also 
uses a rotary potentiometer instead of the trim pot. If there is enough interest, I will make a build guide for it.
Please add at least 100 uF (check voltage rating!) externally to the output, otherwise the feedback loop can be unstable in certain situations.<br> 

Q: &ensp; How reliable is the converter?<br>
A: &ensp; As the converter is being developed on an ongoing basis, it is normal that a few problems may occur at the beginning. Thanks to the practical experience of the last 3 years and iteraton over 6 PCB versions, these problems continue to diminish. To make sure that the converter does not cause any surprises in the field test, there are some tests that I carry out in advance.
Typical tests are:
- UVP/OVP limit tests (test if the voltage protection works properly)
- no load tests (confirm the max. switching frequency)
- full load test for the intended voltage range (check temperatures with themal imaging)
- efficiency test for the intended voltage and load range
- mad scruti test: Try destroying the converter by playing around with the DC/DC enable switch (precharge and turn on/off sequence should be always in safe state)
- hot box test: put the converter inside a small enclosure (2-5l volume) for ≥ 30 mins and record the temperatures inside. A restart should be possible after 30 mins and ≥ 60°C air temperature
- turn-on tests: Monitor switching frequency, inrush currents and voltages (Input/Output/C_r) to confirm that no component limits are exceeded
- Control loop stability test: Apply load jumps and short circuits (!) to the output and observe whether the control loop overshoots and reacts quickly enough
- Miscellaneous: Start capacitor max. start time and long-term storage test (leakage current), Internal power supplies (voltages/currents), Synchronous rectification Waveforms 
- Transformer Isolation Test (> 2kV AC 50 Hz) 
In total there are currently 197 documented tests.
This may sound like a lot, but as this converter is still a work in progress, this effort must be made for every new version and every new build. Once these tests have been passed, some tests no longer need to be carried out (or less strict) for further builds of the same version.
These tests ensure that the converter is very reliable under real conditions. The first converter to pass all the tests (version 8) has been running faultlessly in a racing car for 2 years (and counting). Version 9-2 was installed without a hot-box test based on previous experience ... well, I should have done it once. It turned out later that the converter could no longer reliably start from 55°C upwards due to a OTP measurement problem. A quick-fix solved the problem on the v9-2, a proper solution is installed on the v9-3.<br>

Q: 	&ensp;Why is some text not editable?<br>
A:	&ensp;I like to use a font (Futured) for visuals which is not pre-installed on most systems. 
Importing it as a logo is easier to retain it.<br> 

Q: &ensp;Why are there almost no reference designators on the pcb?<br>
A: &ensp;They do exist! But most of them are hidden below the components. Having them placed around the components looks messy, especially if there is no space left.<br>
For manual assembly, I use the HTML BOM to look up the positions anyway, so I don't really need the designators. At best, I use them for a second look.<br>

Q: 	&ensp;Some 3D models on the PCB are missing.<br>
A:	&ensp;They are not included due to licence terms. However, you can download them from https://www.samacsys.com/ using the Mouser link provided in the properties of the KiCAD components. For quick access: highlight part, press "D".<br>

Q: &ensp;Can a Würth LLC transformer be used instead of a self-wound transformer?<br>
A: &ensp;Physically the footprint does not fit with the current design, but as of v9-3 there would be enough space. Technically you could use them, but their max. power is 200 W and the frequency range is quite different. If one really wants to utilize them, it would be doable. But for now, their limited power is the main reason not to use them.<br>
I'm aware, that building and testing the transformer is might the most complicated part of this whole converter, since it requires tools that not everyone has.
But also think of what learnings and possibilities come from this, so it might be worth the tools, especially if you want to build one every season.

Q: &ensp; KiCAD is throwing lots of errors/warnings on DRC?!  <br>
A: &ensp; This is an expected and desired behaviour. Due to the high voltages on the PCB, I had to ensure that the required clearances were not violated.
Therefore, I created custom rules (.dru file) that assign clearances to critical nets. However, these clearances do not take into account the potential differences. 
So a 600 V net would be 1.2 mm on the outer layers, but the clearance to the high voltage source (612 V) would still be 1.2 mm, even though there is only a 12 V difference.
To solve this correctly, I would have to come up with a rule for the distance between each net. Mathematically, this would be the sum (k) for k = 1 to number_of_all_nets (currently 105), which would give 5565 rules (only for the outer layers, inner layers have different spacing). 
I would like to suggest an integrated KiCAD function that allows to assign voltage potentials to the nets and spacing rules according to the voltage difference.
Until then, I let the most important rules lead to errors and check them all manually.<br>

Q:	&ensp;This is open source. Can I modify it? Can I sell it?<br>
A:	&ensp;Sure! But please use your own version numbering and change "Designed by Rootthecause" 
to "Designed by [Your Name] based on a design by Rootthecause". 
As this is licensed under CeRN OHL v2 Weakly Reciprocal, you must disclose the source, 
state changes and use the same license if used for non private projects.
Learn more about this here: https://choosealicense.com/licenses/cern-ohl-w-2.0/<br>

Q:	&ensp;I've got a question not listed here, can I contact you?<br>
A:	&ensp;Please use the [Discussions](https://github.com/Rootthecause/DCDC/discussions) on GitHub for techical related questions.<br> 

Q:	&ensp;Is there a way to support your projects?<br>
A:	&ensp;Yes, there are two ways: Sharing your findings and results of your own DCDC build as well was financial support for development of this and future projects: https://ko-fi.com/rootthecause<br>
&ensp;&ensp;&ensp; Thanks a lot!

Q: &ensp; I measure something weird [...]<br>
A: &ensp; Make sure that your measuring device is properly isolated. Sometimes small leakage currents can cause unwanted voltages, since we're woking with up to 600V. <br>
Also make sure to use a ground spring when working with an oscilloscope for measuring fast signals.<br>

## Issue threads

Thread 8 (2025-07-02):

Above 575 V Failure

Rootthecause, 2025-07-02:
_Edit: I've moved the release discussion to issues, as it seems more appropriate here, first published June 30, 2025_

An issue with Q11 was found. The exact cause of it's failure is still not fully understood.
Here what's currently known:
- Q11 became permantently conductive when the DCDC operated at above 570V from a HV battery during enabling or applying load
- this failure appeared 2 times on the same DCDC within 3 Days at above 570V but never in the weeks before below 550V
- currently this failure cannot be reproduced with a HV power supply and has not appeared during tests, not even at 605V
- new measurements show, that at 600V input a slight overvoltage between Q11's Drain-Source appear on the rising edge, resulting in 620V seen by the FET. Although the FET is rated for 650V, it is arguably not optimal.
- starting at around 575 V the U_ds rise and fall times drastically increased from 30 ns (575V) to around 60 ns (600V) on Q11 and Q10
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
_Q10 Mesurement, Yellow: Drain-Source Voltage, Purple: Gate-Source Voltage_
- Gate Drive Voltage remains the same
- Previous version (v9-2) operates mostly on the same halfbridge design, but 10 Ohm gate resistors instead of 4.7 Ohm. The resonant circuit is also a bit different. The v9-2 was used as a temporary replacement for v9-3 and did not suffer any failures under similar conditions
- this issue did not occur to another teams's v9-3 replica (yet?)

### Suspected cause (best guesses)
**Gate Resistors**
At first the lower value gate resistors where suspected to cause higher overvoltage due to faster switching. However measurements show, that it only slightly influcences the overvoltage at lower voltages. At 600V input the Drain-Source voltage was 616V at 10 Ohm compared to 619V at 4.7 Ohm.  So this might be not the cause.

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

**Dead-Time**
The weird increase of rise- and fall times above 575V raised the question, whether the dead time was too short. The current dead time was measured at 113 ns (between the outputs of the UCC25600). Increasing it to 180 ns did nothing but increase the current consumption by ~0.3 mA at 500 V (no load). The wave forms and rise/fall times remained the same. The waveforms also did not hint (afaik) to anything that could resemble a halfbidge short due to too low dead time.

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
_Q10 Mesurement, Yellow: Drain-Source Voltage, Red: Drain-Souce Current measured with a rogowski coil (might be not very accurate, just a test)_

**Hard switching**
Although the LLC topology is known for it's soft switching, this is not entirely true depending on input voltage and load.
The primary current waveform transitions with higher input voltage and lower load from a sine to a triangle. This means, that the FETs are switching while current is still conducted, thus being hard switched. This might put load on the FETs while switching, which may result in longer switching times (not sure about this) and higher losses. However, higher losses have not been thermally measured.
Also when enabled, the softstart will begin switching at around 350 kHz. This can also cause hard switching at enable or self restart (e.g. due to overload) → Might be a main cause.

**All of the above**
As the pieces come together, it could be the following picture:
During turn on, the softstart will operate at higher frquencies, causing hard switching and prolonged switching times. The dead time might then be too short, causing a half bridge short (but why only Highside FET damaged?). It is also possible, that the smaller value on the gate resistors are causing the FETs to be switched even harder, causing more thermal stress/EMI/overvoltage. This might be also an issue for the Bootstrap (Diode) - however UVLO of the gate driver should avoid such casualties, but would explain why only the highside FET seems to be affected.

### Solution
As the mystery is not fully solved, the following changes were made as a first attempt:
- Changed gate resistors R56/R58 from 4.7 Ohm to 10 Ohm
- Increased dead time to 180 ns (can be measured beween Pin 8 and 5 at U12, measure the time at 0V)
- ordered FETs with higher breakdown Voltage: [750V](https://www.mouser.de/ProductDetail/Infineon-Technologies/AIMBG75R090M1HXTMA1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) and [1200V](https://www.mouser.de/ProductDetail/Infineon-Technologies/IMBG120R220M1HXTMA1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)
Note: The 750V has lower switching losses than the 1200V version. I will go with the 750V version first.

For now, the first tests will be conducted with the current 650V FETs but with altered dead time and 10 Ohm gate resistors.

Rootthecause, 2025-07-02:
_Update July 2, 2025_

Despite working for multiple days on this issue, I have not figured out how to solve it. However, there are some new measurements, which might explain some things.

**Hard Switching**
As hard switching only depends on the switching frequency, but not the input voltage, it should be possible to see prolonged switching times at voltages way below normal operation. A measurement at 50 V input voltage confirmed this.

With rising Input voltage, the switching times decreased, which does make sense, as Coss decreases.

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<br> _Capacitances for the currently used IMBG65R050M2HXTMA1_

The Gate Driver and highside bootstrap could be ruled out as a source of the problems. There was a slight decrease in the highside supply voltage from 11.7 V (90 kHz switching frequency) to 11.2 V (320 kHz) measured. Despite of SiC MOSFETs Rds_on are more dependend on gate voltage than Si, this small change should not have an impact this large on the switching times.

Currently the main cause of failure might be the too long switching times due to hard switching. This would require an increased dead time. Unfortunately, even increasing the dead time from 180 ns to 370 ns lead to a failure. This time, for the first time, on the workbench. Luckly I got the scope connected and captured the whole event (RAW data available).

The following images show the Drain Source voltage of the low side FET, which is also the Halfbrige output voltage or the negative voltage of the highside Drain source (Source-Drain if you wish).

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

The beginning is quite normal for this topology: Switching until the Bootstrap capacitor is charged up, which then enables the highside FET for normal operation. However, despite of the 600V input source, somehow there are 800V peak already. Even weirder: there are up to -200V ?!?!!. HOW!? The oscilloscope was battery powered and the probe is accurate too. Those are not just transients, as can be seen here:

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

The Dutycycle which is normally at 50% (± dead time) was at 65%. This could be a result of the dead time being at 370 ns, but somehow this looks wrong to me. I would expect less than 50%.

Later in the event, something caused the DS Voltage starting to rise earlier, until a half bridge short persumably happened.

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

Leading to a failure of the lowside FET.

**Solution?**
All of this might be a result of the hard switching. So the new plan is to avoid hard switching alltogether.
Calculations of the current resonant design showed, that above 180 kHz (gain = 1) hard switching would happen. Decreasing the resonant capacitor from 22.4 nF to 12 nF should increase it to 240 kHz.

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

The measurement revealed, that the impact was way lower than expected: The difference for the same rise times were 25 kHz at best and not 60 kHz. Also note, that the second datapoint for 12 nF (blue) is close to the highest gain, whereas the first datapoint is below this, switching in the capacitive (forbidden) region, as this region is considered as hard switching. Despite this, the rise time was even lower!

Btw. the C0G capacitors (C_res) retained their original capacitance after the failure. Using a film capacitor and single capacitor to ground instead of split capacitors does also not change anything. In 2 out of 4 failures one C0G capacitor failed as well, so have them in stock! I assume they are failing due to the sudden FET failures (4 out of 4 times), and not the FET failing due to the G0G.

So no, currently I don't know any solution. It does make even less sense now. Send help.

If your replica still works at 600V, let me know what your secret is.

Rootthecause, 2025-07-18:
_July 18, 2025_
Updated Build Guide with recommended test voltages for mimimum switching frequency setting.

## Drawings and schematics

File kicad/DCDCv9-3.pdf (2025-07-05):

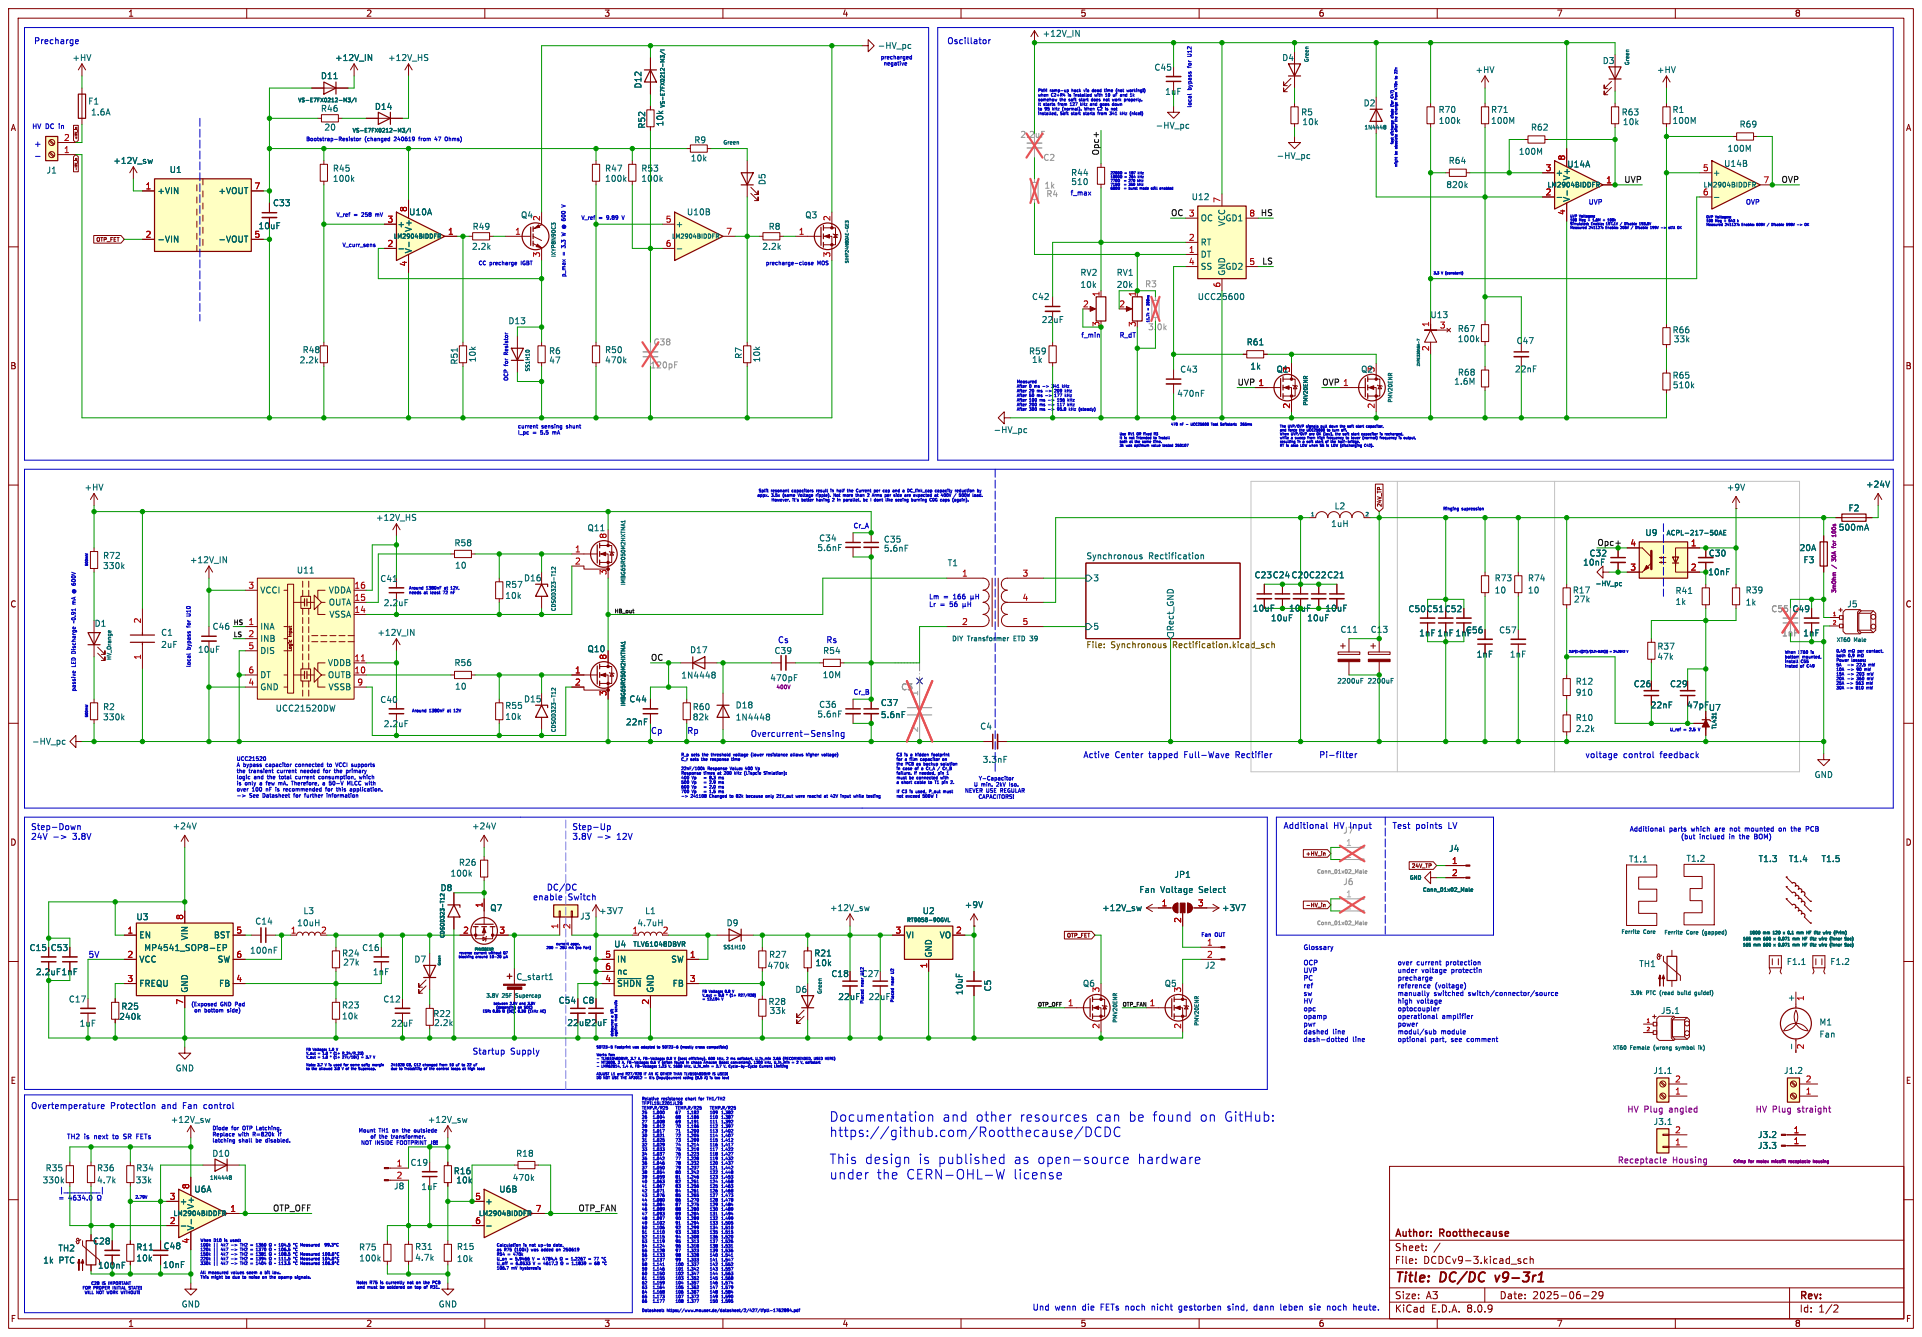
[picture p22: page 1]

HV DC in Precharge

OVP HS UVP OC

(but inclued in the BOM) U_ref = 2.5 V 500mW

3.9k PTC (read build guide!) R2

Y-Capacitor U min. 2kV Iso. NEVER USE REGULAR

https://github.com/Rootthecause/DCDC

2.79V TH2 is next to SR FETs

of the transformer. NOT INSIDE FOOTPRINT J8!

C28 IS IMPORTANT
FOR PROPER INITIAL STATE! WILL NOT WORK WITHOUT!

Id: 1/2 Title: DC/DC v9-3r1

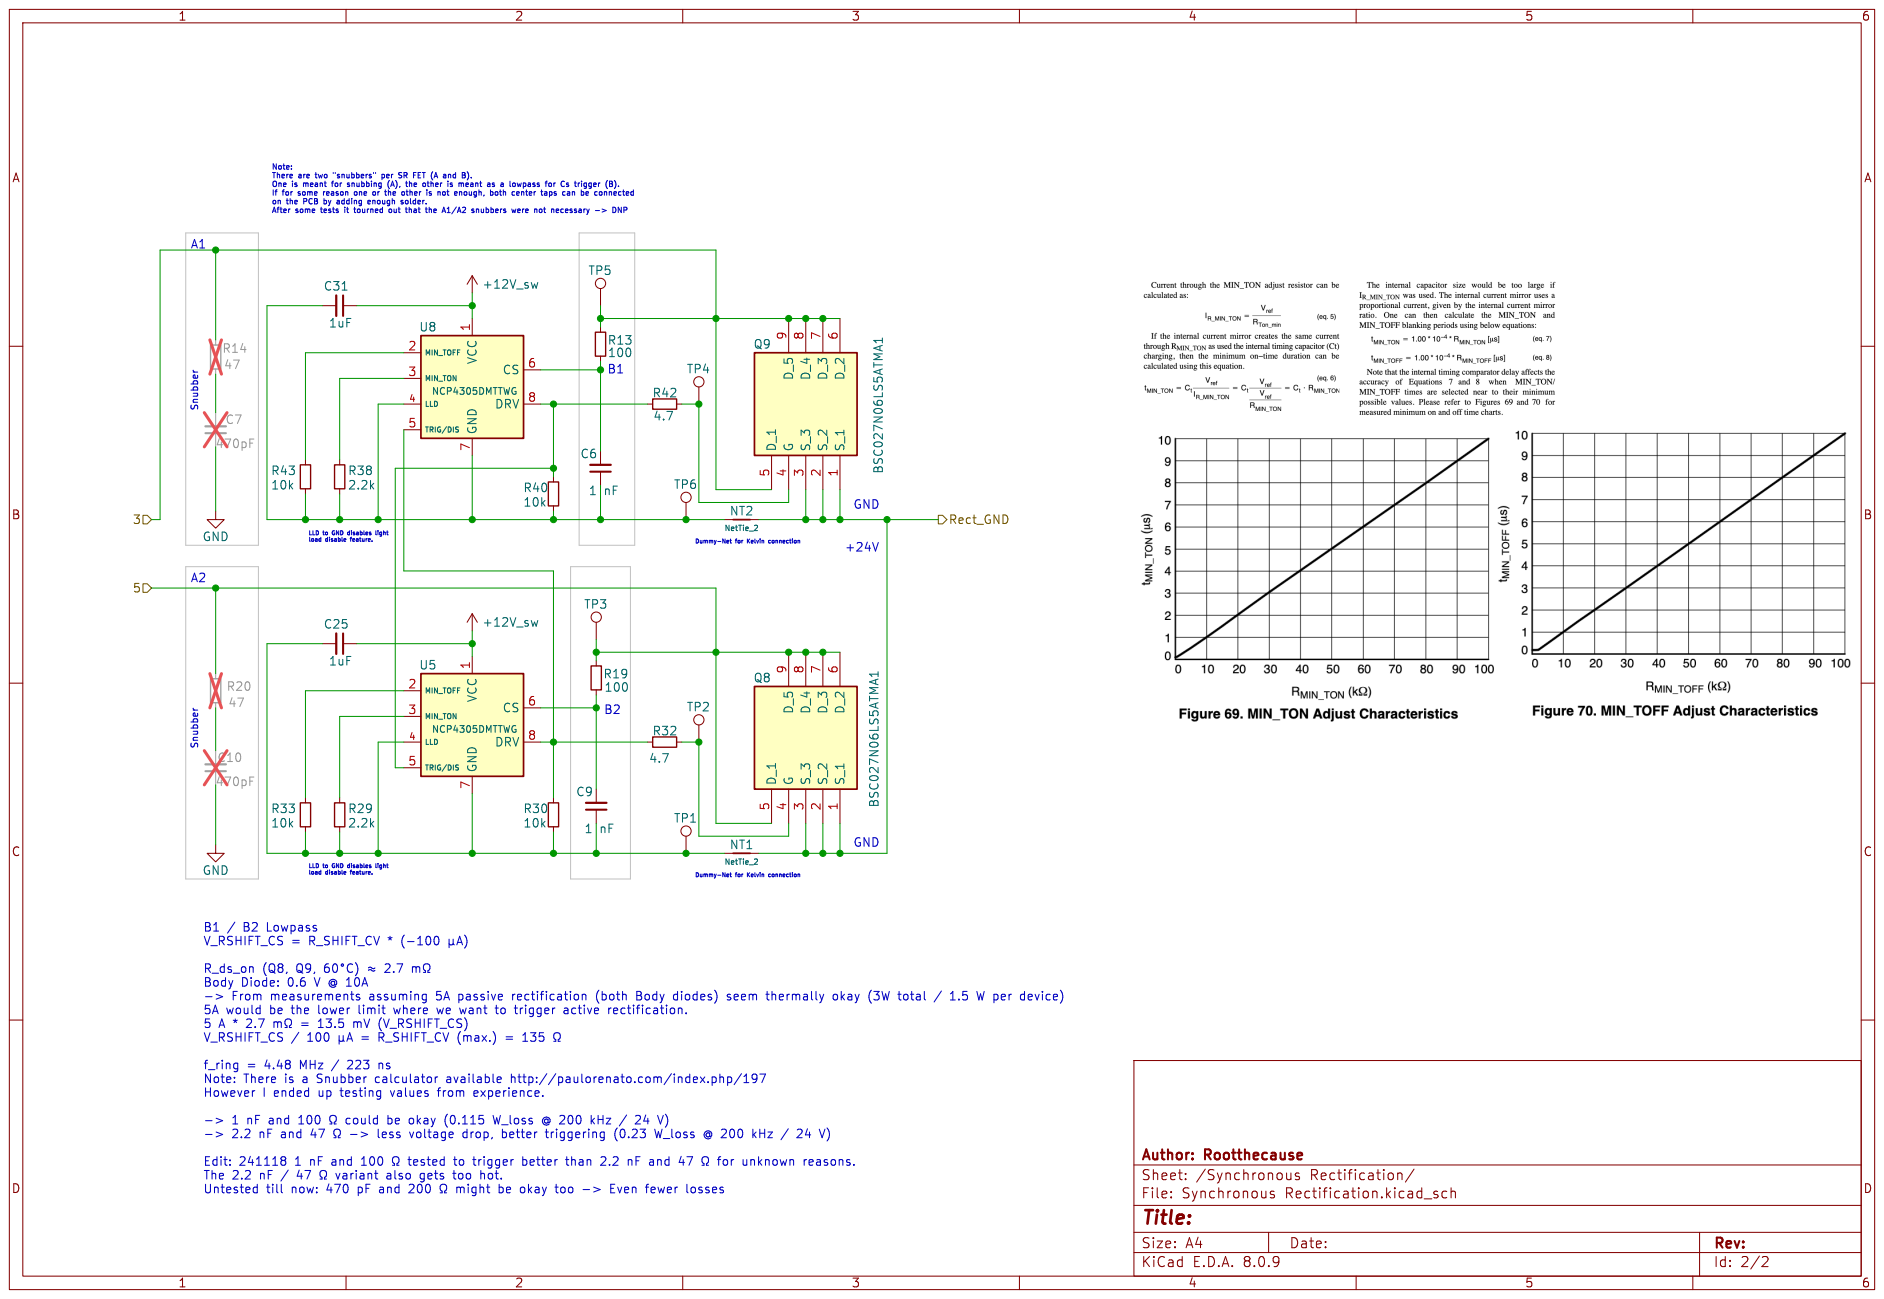
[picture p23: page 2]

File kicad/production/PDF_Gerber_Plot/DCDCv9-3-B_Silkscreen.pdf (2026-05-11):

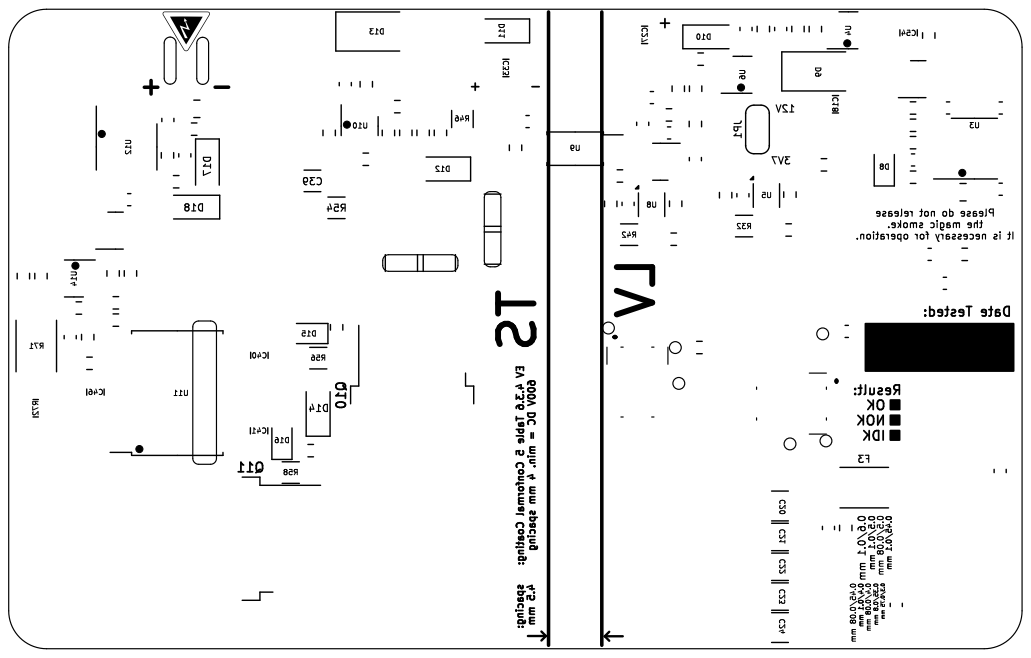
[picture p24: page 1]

smoke. magic the operation. for necessary is It 0.3/0.75 mm - + 0.35/0.8 mm Result: EV 4.3.6 Table 5 Conformal Coating: 600V DC = min. 4 mm spacing

release not do Please

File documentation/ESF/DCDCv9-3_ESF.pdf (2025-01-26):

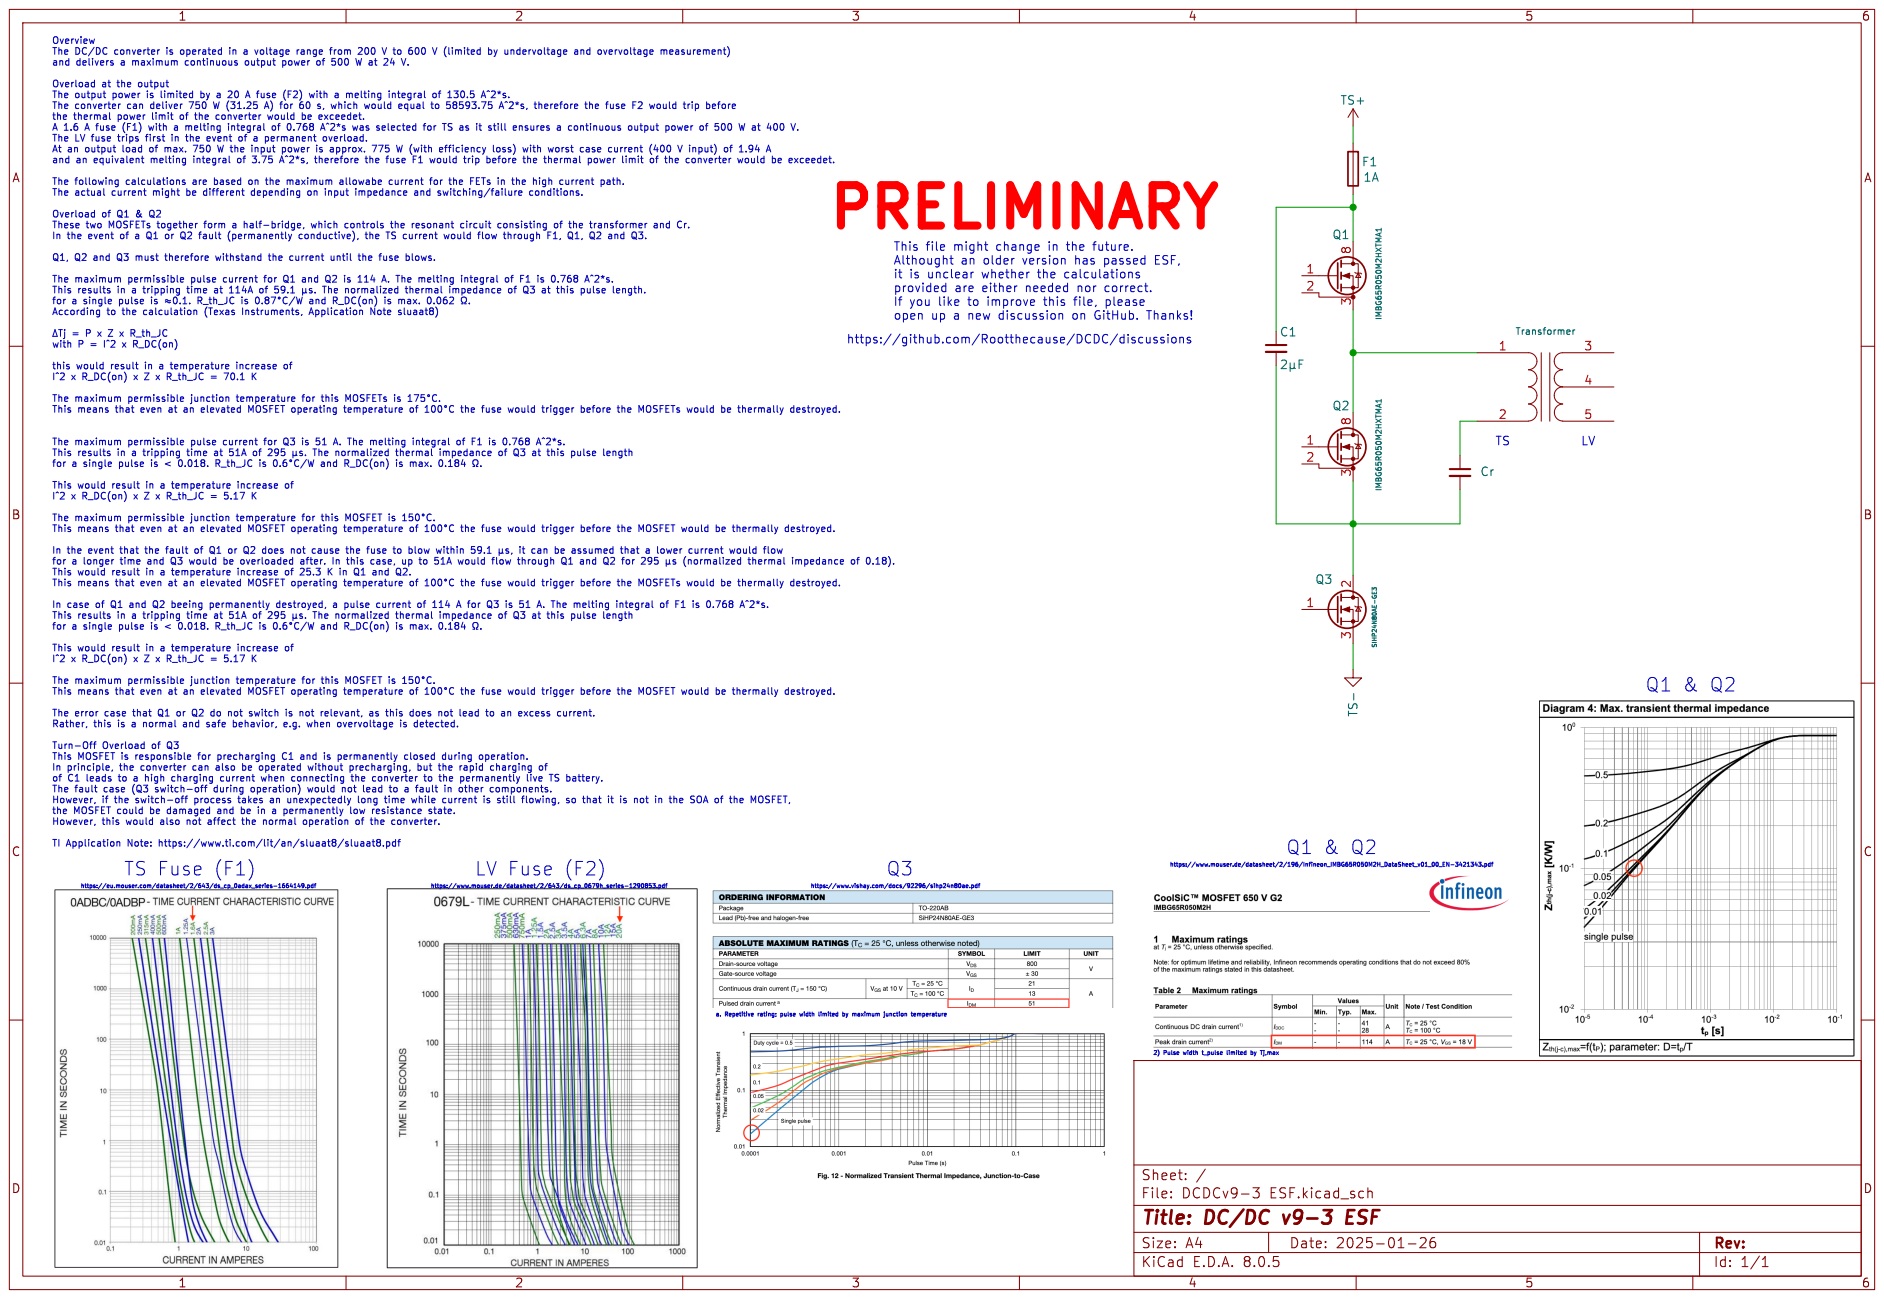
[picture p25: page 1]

it is unclear whether the calculations provided are either needed nor correct.

If you like to improve this file, please

https://github.com/Rootthecause/DCDC/discussions

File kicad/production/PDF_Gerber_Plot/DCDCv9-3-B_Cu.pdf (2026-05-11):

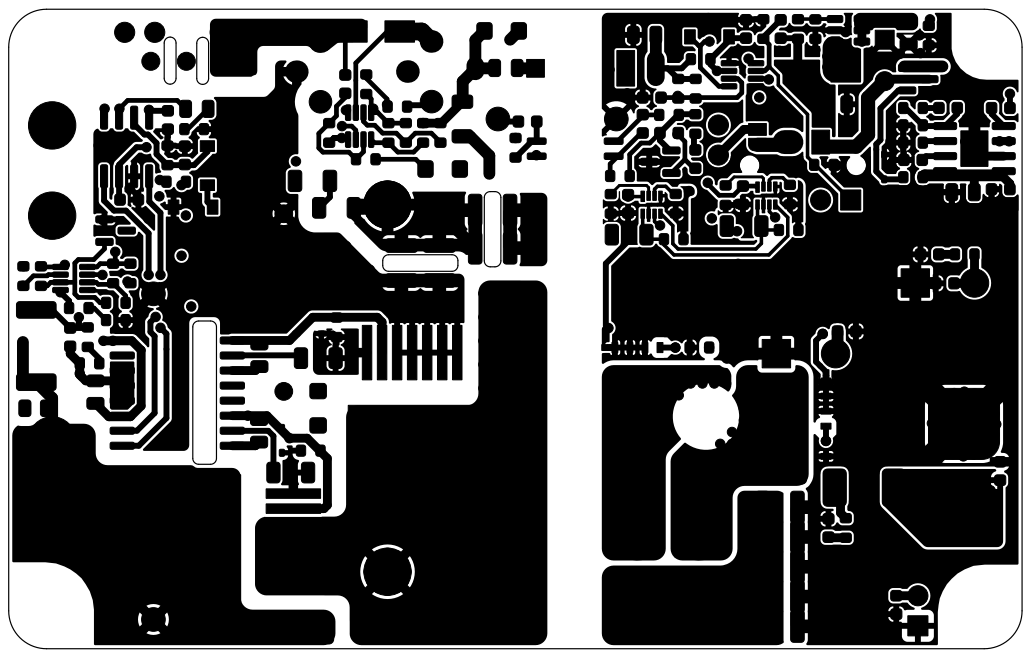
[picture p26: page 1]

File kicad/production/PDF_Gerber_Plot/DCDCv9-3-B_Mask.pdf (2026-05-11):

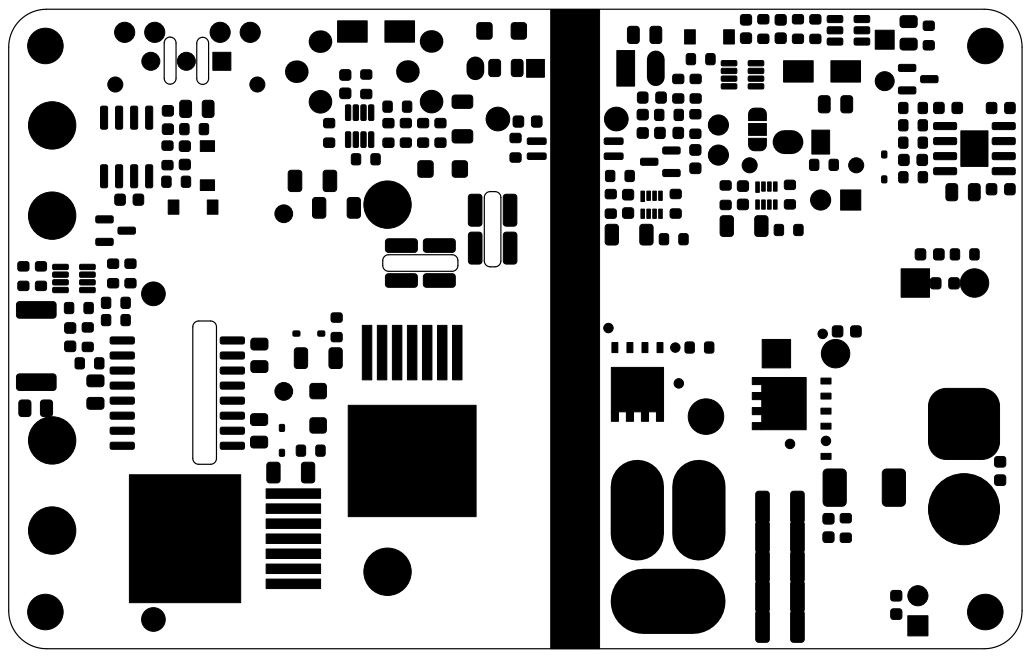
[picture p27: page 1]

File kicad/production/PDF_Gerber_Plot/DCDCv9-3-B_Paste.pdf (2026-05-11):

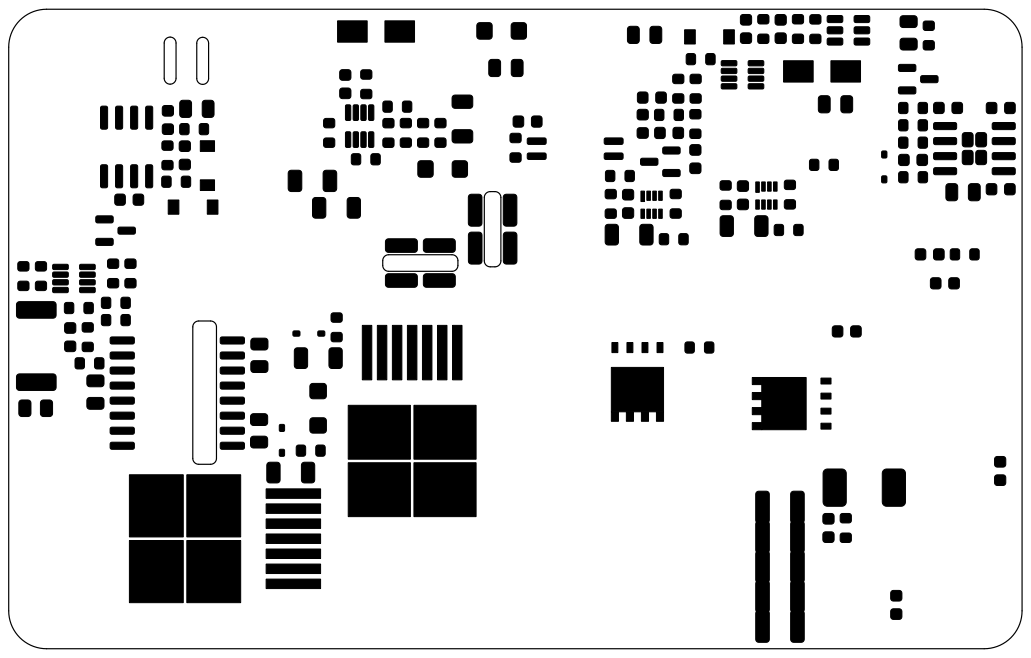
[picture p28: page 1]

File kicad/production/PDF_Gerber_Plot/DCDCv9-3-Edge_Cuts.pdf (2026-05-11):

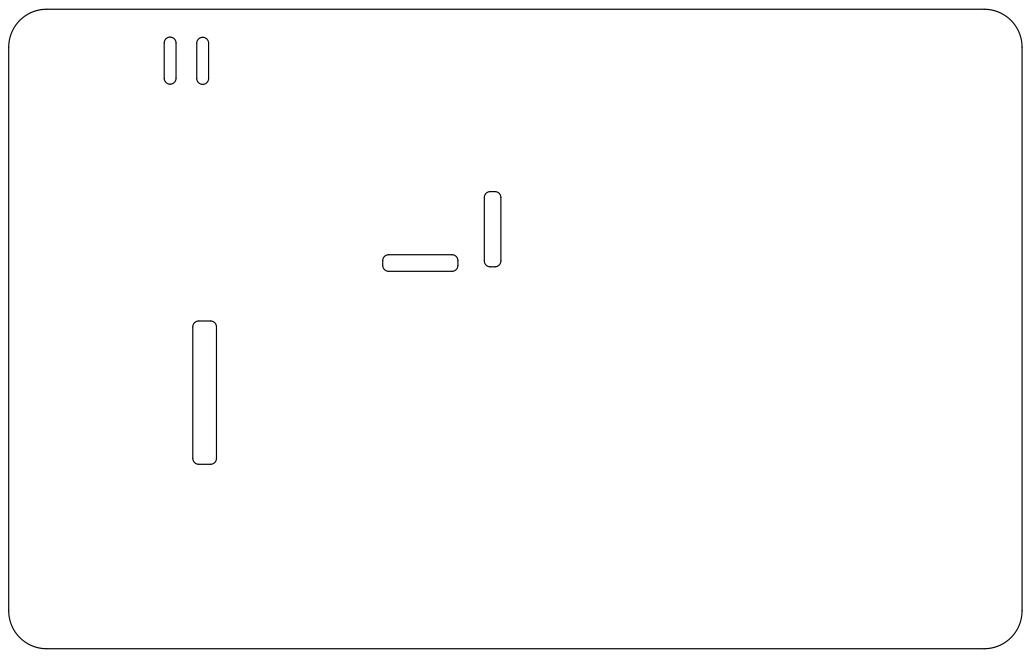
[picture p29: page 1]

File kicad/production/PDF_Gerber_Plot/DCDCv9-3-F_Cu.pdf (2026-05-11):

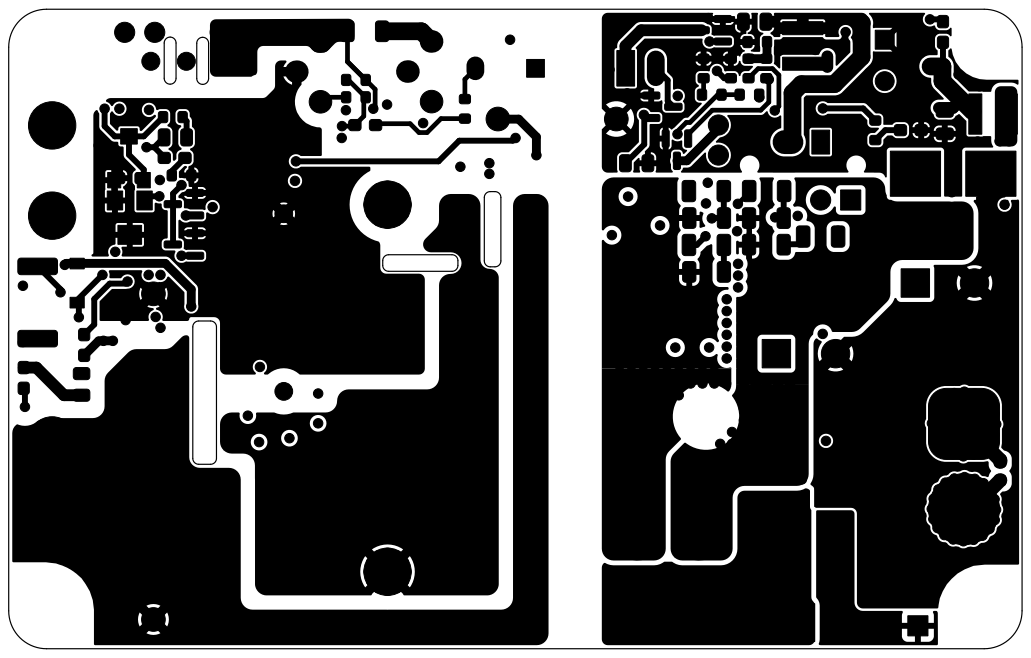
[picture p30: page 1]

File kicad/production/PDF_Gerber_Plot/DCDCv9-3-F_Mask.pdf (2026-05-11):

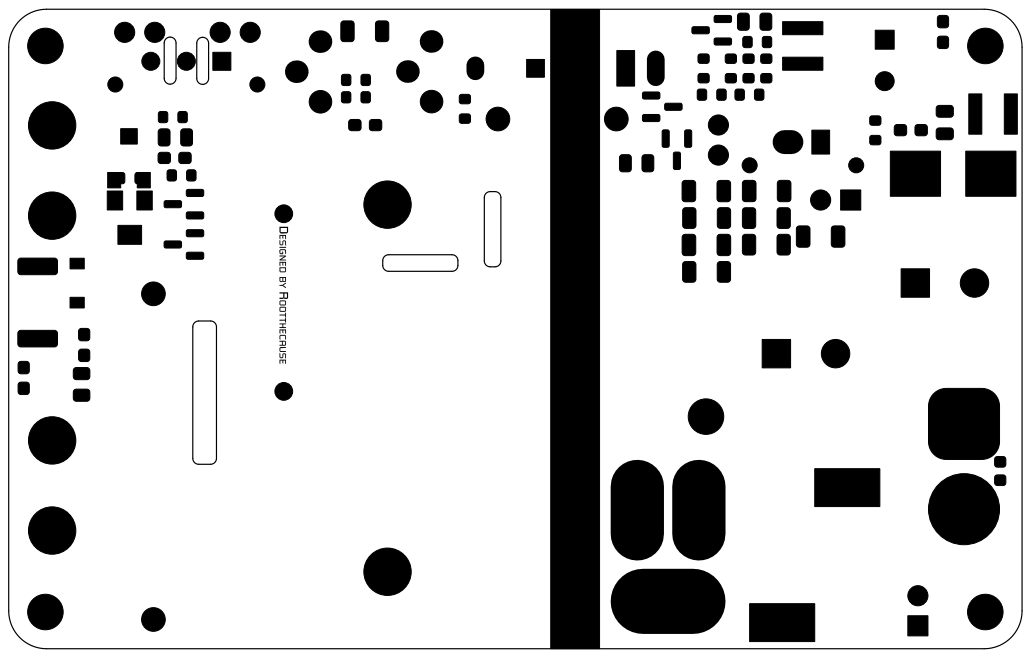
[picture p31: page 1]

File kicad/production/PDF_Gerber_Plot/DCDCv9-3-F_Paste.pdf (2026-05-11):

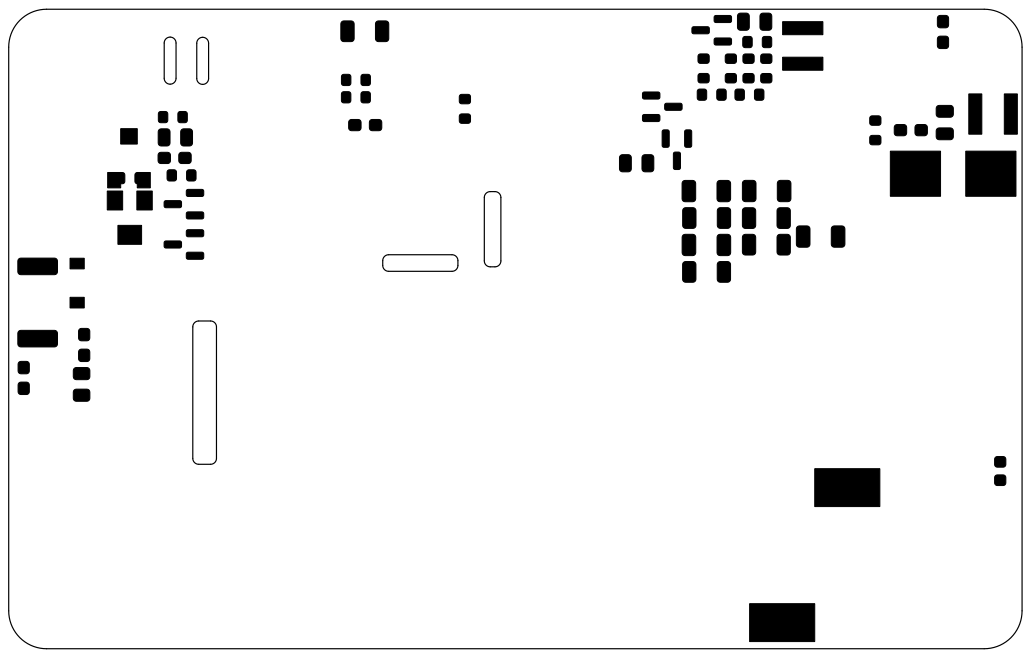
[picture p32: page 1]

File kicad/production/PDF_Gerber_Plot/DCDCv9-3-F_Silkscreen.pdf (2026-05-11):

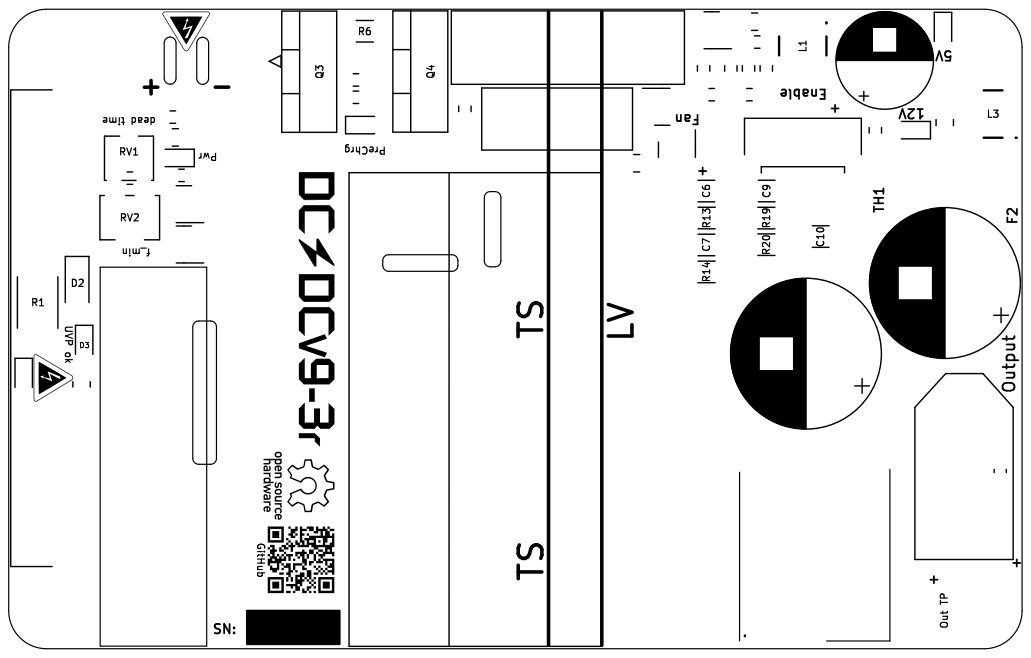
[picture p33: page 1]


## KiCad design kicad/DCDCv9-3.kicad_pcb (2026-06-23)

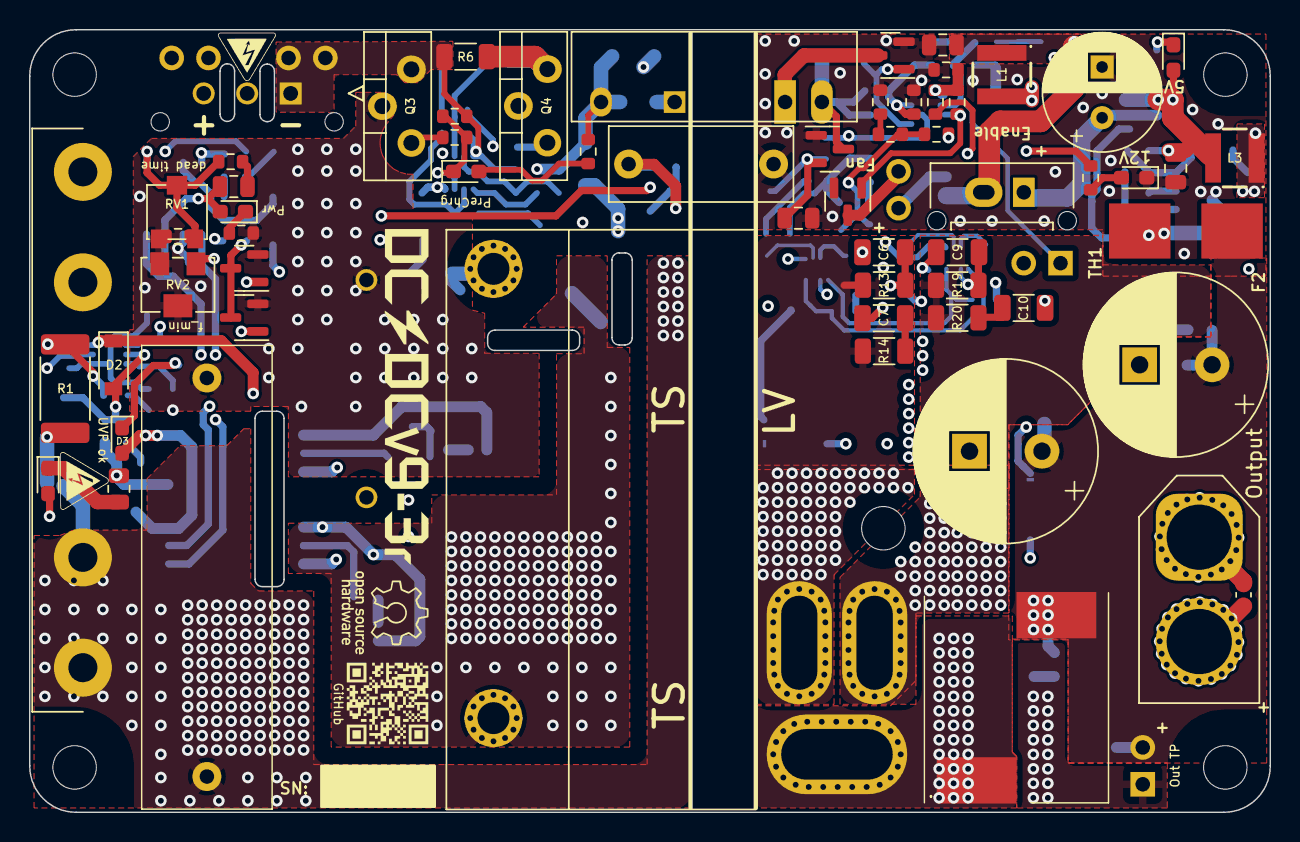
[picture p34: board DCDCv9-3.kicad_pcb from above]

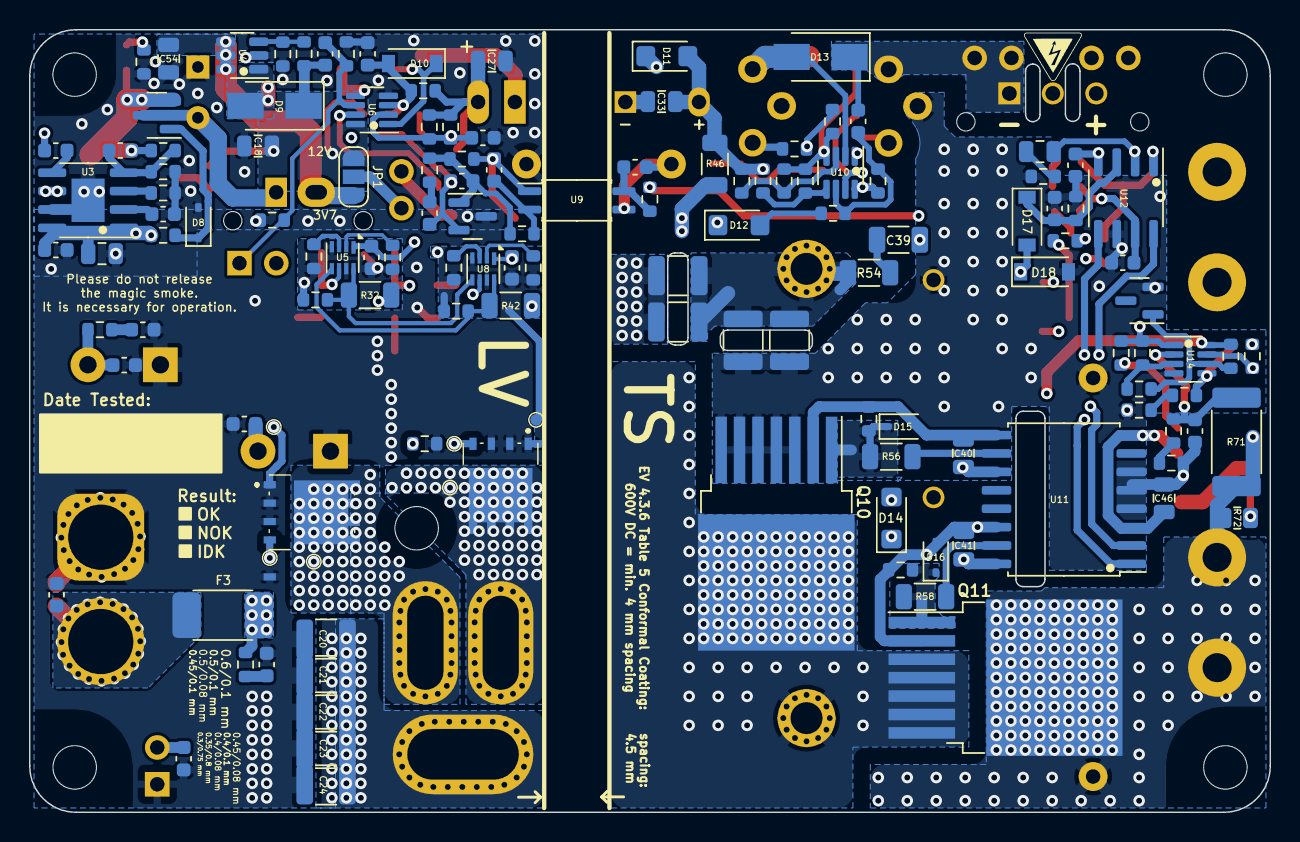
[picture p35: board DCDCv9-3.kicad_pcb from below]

Board: 4 copper layers, 85.6 x 54.0 mm, 208 parts (140 on the bottom side), 102 nets.

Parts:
C1: 2uF; MKP1848520704K2
C2, C15, C40, C41: 2.2uF; C_0805_2012Metric
C3: 22nF; R76UI22205050J
C4: 3.3nF; C_Disc_D12.5mm_W5.0mm_P10.00mm
C5, C33, C46: 10uF; C_0805_2012Metric
C6, C9: 1 nF; C_1206_3216Metric
C7, C10, C39: 470pF; C_1206_3216Metric
C8, C12, C18, C27, C42, C54: 22uF; C_0805_2012Metric
C11, C13: 2200uF; CP_Radial_D12.5mm_P5.00mm_symbol_inside
C14, C28: 100nF; C_0603_1608Metric
C16, C49, C50, C51, C52, C53, C55, C56, C57: 1nF; C_0603_1608Metric
C17, C19, C25, C31, C45: 1uF; C_0603_1608Metric
C20, C21, C22, C23, C24: 10uF; C_1210_3225Metric
C26, C44, C47: 22nF; C_0603_1608Metric
C29: 47pF; C_0603_1608Metric
C30, C32, C48: 10nF; C_0603_1608Metric
C34, C35, C36, C37: 5.6nF; C_1210_3225Metric
C38: 120pF; C_0603_1608Metric
C43: 470nF; C_0603_1608Metric
C_start1: 3.8V 25F Supercap; CP_Radial_D8.0mm_P3.50mm
D1: HV_Orange; LED_0603_1608Metric_Pad1.05x0.95mm_HandSolder
D2, D10, D17, D18: 1N4448; D_SOD-123
D3, D4, D5, D6, D7: Green; LED_0603_1608Metric_Pad1.05x0.95mm_HandSolder
D8, D15, D16: CDSOD323-T12; D_SOD-323
D9, D13: SS1H10; D_SMA
D11, D12, D14: VS-E7FX0212-M3/I; D_SMF
F1: 1.6A; Fuseholder0,25Zoll_32mm_littlefuse_102_122
F2: 500mA; NANO-0154-OMNI-BLOK-Fuse-Holder
F3: 20A; Bel_SMCF_Fuse_2410_6125Metric
HV_Logo_1, HV_Logo_1#2, HV_Logo_1#3: HV_Logo_1; HV_Logo_small
J1: 43650-0315; 43650-03YY_151617
J2, J4, J6, J7, J8: Conn_01x02_Male; PinHeader_1x02_P2.54mm_Vertical
J3: Conn_01x02; Molex_Micro-Fit_3.0_43650-0215_1x02_P3.00mm_Vertical_combin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
J5: XT60 Male; AMASS_XT60-F_1x02_P7.20mm_Vertical
JP1: Fan Voltage Select; SolderJumper-3_P1.3mm_Open_RoundedPad1.0x1.5mm_NumberLabels
L1: 4.7uH; ASPI-4030S
L2: 1uH; 7443091100_v9.2
L3: 10uH; ASPI-4030S
NT1, NT2: NetTie_2; dummy_net_line_0.5mm
Q1, Q2, Q5, Q6, Q7: PMV20ENR; SOT-23
Q3: SIHP24N80AE-GE3; TO-220-3_Vertical_HV1.2mm
Q4: IXYP8N90C3; TO-220-3_Vertical_HV1.2mm
Q8, Q9: BSC027N06LS5ATMA1
Q10, Q11: IMBG65R050M2HXTMA1; TO-263-7_TabPin8
QR_Coode_1: QR_Coode; GitHub_QR_Code
R1, R71: 100M; R_2512_6332Metric_Pad1.40x3.35mm_HandSolder
R2, R72: 330k; R_0805_2012Metric
R3: 3.0k; R_0603_1608Metric
R4, R39, R41, R59, R61: 1k; R_0603_1608Metric
R5, R7, R9, R11, R15, R16, R21, R23, R30, R33, R40, R43, R51, R52, R55, R57, R63: 10k; R_0603_1608Metric
R6, R14, R20: 47; R_1206_3216Metric
R8, R10, R22, R29, R38, R48, R49: 2.2k; R_0603_1608Metric
R12: 910; R_0603_1608Metric
R13, R19: 100; R_1206_3216Metric
R17, R24: 27k; R_0603_1608Metric
R18, R27, R50: 470k; R_0603_1608Metric
R25: 240k; R_0603_1608Metric
R26, R45, R47, R53, R67, R70, R75: 100k; R_0603_1608Metric
R28, R34, R66: 33k; R_0603_1608Metric
R31, R36: 4.7k; R_0603_1608Metric
R32, R42: 4.7; R_1206_3216Metric
R35: 330k; R_0603_1608Metric
R37: 47k; R_0603_1608Metric
R44: 510; R_0603_1608Metric
R46: 20; R_1206_3216Metric
R54: 10M; R_1206_3216Metric
R56, R58: 10; R_1206_3216Metric
R60: 82k; R_0603_1608Metric
R62, R69: 100M; R_0603_1608Metric
R64: 820k; R_0603_1608Metric
R65: 510k; R_0603_1608Metric
R68: 1.6M; R_0603_1608Metric
R73, R74: 10; R_0603_1608Metric
RV1: 20k; Potentiometer_Bourns_PVG3G
RV2: 10k; Potentiometer_Bourns_3214W_Vertical
T1: DIY Transformer ETD 39; Transformer_ETD39_uprightV3.6 (PSS 24V)
TH2: 1k PTC; R_0603_1608Metric
TP1, TP2, TP3, TP4, TP5, TP6: TestPoint; TestPoint_Pad_D0.8mm_DC-DC
TP8: GaN GND2; TestPoint_Pad_D0.8mm_DC-DC
U1: RP-1212S; Converter_DCDC_TRACO_TBA 1-1212HI-3kV-iso
U2: RT9058-90GVL; SOT-23
U3: MP4541_SOP8-EP; SOIC-8-1EP_3.9x4.9mm_P1.27mm_EP2.29x3mm XL7005
U4: TLV61048DBVR; SOT-23-6
U5, U8: NCP4305DMTTWG; WDFN-8_2x2mm_P0.5mm
U6, U10, U14: LM2904BIDDFR; SOT-23-8_DC-DC_v9
U7: TL431BCDBZR; SOT-23
U9: ACPL-217-50AE; SOIC-4_4.55x2.6mm_P1.27mm
U11: UCC21520DW; SOIC-16W_7.5x10.3mm_P1.27mm
U12: UCC25600; SOIC-8_3.9x4.9mm_P1.27mm
U13: ZXRE330ASA-7; SOT-23

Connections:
24V_TP: C11.1, C13.1, C50.2, C51.2, C52.2, F2.1, F3.1, J4.1, L2.2, R17.1, R73.1, R74.1
+3V7: C8.1, C54.1, J3.2, JP1.3 (B), L1.1, U4.4 (~SHDN), U4.5 (IN), U4.6 (nc)
+9V: C5.1, C30.2, R39.1, U2.2 (VO), U9.1
+12V_HS: C41.2, D14.1 (K), U11.16 (VDDA)
+12V_IN: C2.2, C40.2, C45.2, C46.1, D2.1 (K), D3.2 (A), D4.2 (A), D11.1 (K), R70.1, U11.3 (VCCI), U11.8 (VCCI), U11.11 (VDDB), U12.7 (VCC), U14.8 (V+)
+12V_sw: C18.1, C19.2, C25.1, C27.1, C31.1, D9.1 (K), J8.1, JP1.1 (A), R16.1, R21.2, R27.1, R34.1, R35.2, R36.2, U1.1 (+VIN), U2.3 (VI), U5.1 (VCC), U6.8 (V+), U8.1 (VCC)
+24V: C15.2, C53.2, F2.2, R26.2, U3.1 (EN), U3.8 (VIN)
+HV: C1.2, C34.1, C35.1, F1.2, Q11.8 (D), R1.1, R71.1, R72.1
+HV_in: F1.1, J1.3, J7.1, J7.2
-HV_in: C33.2, C38.1, D13.1 (K), J1.1, J6.1, J6.2, Q3.3 (S), R6.2, R7.2, R48.1, R50.1, R51.2, U1.5 (-VOUT), U10.4 (V-)
-HV_pc: C1.1, C3.2, C4.1, C32.2, C36.2, C37.2, C43.2, C44.1, C45.1, C46.2, C47.2, D12.1 (K), D18.2 (A), Q1.2 (S), Q2.2 (S), Q3.2 (D), Q4.2 (C), Q10.3 (S), Q10.4 (S), Q10.5 (S), Q10.6 (S), Q10.7 (S), R2.2, R3.2, R5.1, R59.2, R60.1, R65.2, R68.2, RV1.3, RV2.2, RV2.3, U9.3, U11.4 (GND), U11.5 (DIS), U11.6 (DT), U12.6 (GND), U13.2, U14.4 (V-)
/HB_out: Q10.8 (D), Q11.3 (S), Q11.4 (S), Q11.5 (S), Q11.6 (S), Q11.7 (S), T1.1 (AA)
/HS: U11.1 (INA), U12.8 (GD1)
/LS: U11.2 (INB), U12.5 (GD2)
/OC: C44.2, D17.1 (K), R60.2, U12.3 (OC)
/OTP_FAN: Q5.1 (G), R18.1, U6.7
/OTP_OFF: D10.1 (K), Q6.1 (G), U6.1
/OVP: Q2.1 (G), R69.1, U14.7
/Opc+: C32.1, R44.2, U9.4
/Synchronous Rectification/3: Q9.5 (D_1), Q9.6 (D_2), Q9.7 (D_3), Q9.8 (D_4), Q9.9 (D_5), R13.2, R14.1, T1.3 (SB), TP5.1
/Synchronous Rectification/5: Q8.5 (D_1), Q8.6 (D_2), Q8.7 (D_3), Q8.8 (D_4), Q8.9 (D_5), R19.2, R20.1, T1.5 (SA), TP3.1
/UVP: Q1.1 (G), R62.1, R63.1, U14.1
GND: C4.2, C5.2, C7.1, C8.2, C10.1, C11.2, C12.1, C13.2, C15.1, C17.1, C18.2, C20.2, C21.2, C22.2, C23.2, C24.2, C27.2, C28.1, C48.1, C49.1, C50.1, C51.1, C52.1, C53.1, C54.2, C55.1, C56.1, C57.1, C_start1.2 (-), D6.1 (K), D8.2 (A2), J4.2, J5.2, NT1.2, NT2.2, Q5.2 (S), Q6.2 (S), Q8.1 (S_1), Q8.2 (S_2), Q8.3 (S_3), Q9.1 (S_1), Q9.2 (S_2), Q9.3 (S_3), R10.2, R11.2, R15.1, R22.1, R23.2, R25.1, R28.2, R31.1, R75.2, TH2.2, TP8.1, U2.1 (GND), U3.7 (GND), U4.2 (GND), U6.4 (V-), U7.3 (A)
unnamed: C2.1, R4.2
unnamed: C7.2, R14.2
unnamed: C10.2, R20.2
unnamed: C26.2, R37.1
unnamed: C30.1, R41.1, U9.2
unnamed: C39.2, R54.1
unnamed: C42.2, R59.1
unnamed: C56.2, R73.2
unnamed: C57.2, R74.2
unnamed: C_start1.1 (+), J3.1, Q7.3 (D)
unnamed: D1.2 (A), R72.2
unnamed: D1.1 (K), R2.1
unnamed: C47.1, D2.2 (A), R67.2, R71.2, U14.2 (-)
unnamed: D3.1 (K), R63.2
unnamed: D4.1 (K), R5.2
unnamed: D5.2 (A), R9.1
unnamed: D5.1 (K), R7.1, R8.2, U10.7
unnamed: D6.2 (A), R21.1
unnamed: C12.2, C16.2, D7.2 (A), L3.2, Q7.2 (S), R24.1
unnamed: D7.1 (K), R22.2
unnamed: D8.1 (A1), Q7.1 (G), R26.1
unnamed: D9.2 (A), L1.2, U4.1 (SW)
unnamed: C48.2, D10.2 (A), R11.1, R34.2, U6.3 (+)
unnamed: C33.1, D11.2 (A), R9.2, R45.2, R46.2, R47.2, R53.2, U1.7 (+VOUT), U10.8 (V+)
unnamed: D12.2 (A), R52.1
unnamed: D13.2 (A), Q4.3 (E), R6.1, U10.2 (-)
unnamed: D14.2 (A), R46.1
unnamed: D15.1 (A1), Q10.1 (G), R55.1, R56.1
unnamed: C40.1, D15.2 (A2), Q10.2 (DS), R55.2, U11.9 (VSSB)
unnamed: D16.1 (A1), Q11.1 (G), R57.1, R58.1
unnamed: C41.1, D16.2 (A2), Q11.2 (DS), R57.2, U11.14 (VSSA)
unnamed: C39.1, D17.2 (A), D18.1 (K)
unnamed: J2.1, JP1.2 (C)
unnamed: J2.2, Q5.3 (D)
unnamed: C49.2, C55.2, F3.2, J5.1
unnamed: C19.1, J8.2, R31.2, R75.1, U6.6 (-)
unnamed: Q1.3 (D), Q2.3 (D), R61.1
unnamed: Q3.1 (G), R8.1
unnamed: Q4.1 (G), R49.1
unnamed: Q8.4 (G), R32.1, TP2.1
unnamed: Q9.4 (G), R42.1, TP4.1
unnamed: R10.1, R12.2
unnamed: R49.2, R51.1, U10.1
unnamed: R65.1, R66.2
unnamed: R67.1, R68.1
unnamed: C34.2, C35.2, C36.1, C37.1, R54.2, T1.2 (AB)
unnamed: C20.1, C21.1, C22.1, C23.1, C24.1, L2.1, T1.4 (SC)
unnamed: C14.2, U3.5 (BST)
unnamed: C16.1, R23.1, R24.2, U3.4 (FB)
unnamed: R25.2, U3.3 (FREQU)
unnamed: C14.1, L3.1, U3.6 (SW)
unnamed: C17.2, U3.2 (VCC)
unnamed: R27.2, R28.1, U4.3 (FB)
unnamed: C9.2, R19.1, U5.6 (CS)
unnamed: R30.2, R32.2, U5.8 (DRV), U8.5 (TRIG/DIS)
unnamed: C9.1, C25.2, NT1.1, R29.1, R30.1, R33.1, TP1.1, U5.4 (LLD), U5.7 (GND)
unnamed: R33.2, U5.2 (MIN_TOFF)
unnamed: R29.2, U5.3 (MIN_TON)
unnamed: R40.2, R42.2, U5.5 (TRIG/DIS), U8.8 (DRV)
unnamed: C28.2, R35.1, R36.1, TH2.1, U6.2 (-)
unnamed: R15.2, R16.2, R18.2, U6.5 (+)
unnamed: C29.2, R37.2, R39.2, R41.2, U7.1 (K)
unnamed: C26.1, C29.1, R12.1, R17.2, U7.2 (REF)
unnamed: C6.2, R13.1, U8.6 (CS)
unnamed: C6.1, C31.2, NT2.1, R38.1, R40.1, R43.1, TP6.1, U8.4 (LLD), U8.7 (GND)
unnamed: R43.2, U8.2 (MIN_TOFF)
unnamed: R38.2, U8.3 (MIN_TON)
unnamed: R45.1, R48.2, U10.3 (+)
unnamed: R47.1, R50.2, U10.5 (+)
unnamed: C38.2, R52.2, R53.1, U10.6 (-)
unnamed: R58.2, U11.15 (OUTA)
unnamed: R56.2, U11.10 (OUTB)
unnamed: R3.1, R4.1, RV1.1, RV1.2, U12.1 (DT)
unnamed: C42.1, R44.1, RV2.1, U12.2 (RT)
unnamed: C43.1, R61.2, U12.4 (SS)
unnamed: R62.2, R64.1, U14.3 (+)
unnamed: R1.2, R66.1, R69.2, U14.5 (+)
unnamed: R64.2, R70.2, U13.1, U14.6 (-)
OTP_FET: Q6.3 (D), U1.2 (-VIN)

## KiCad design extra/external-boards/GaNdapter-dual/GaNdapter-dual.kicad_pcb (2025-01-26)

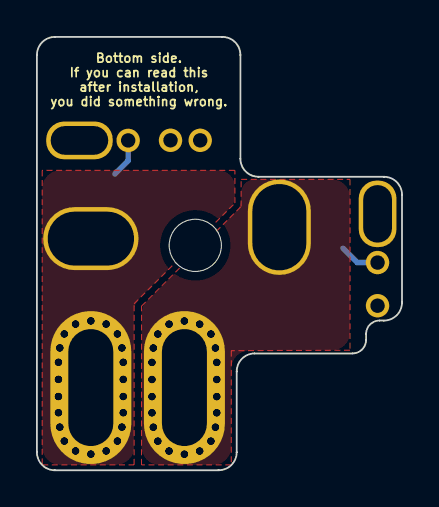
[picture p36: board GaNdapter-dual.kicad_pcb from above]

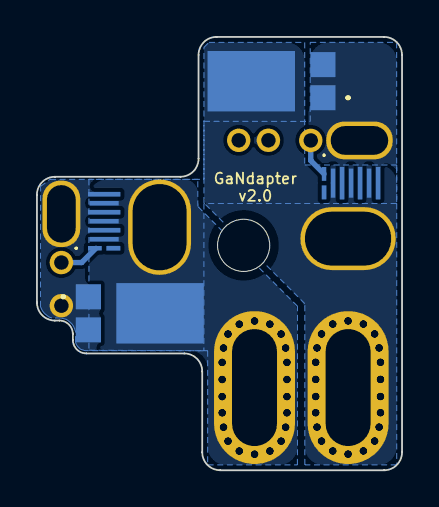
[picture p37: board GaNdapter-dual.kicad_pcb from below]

Board: 2 copper layers, 20.3 x 24.1 mm, 12 parts (4 on the bottom side), 5 nets.

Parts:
D1, D2: SBR10U200P5-13; SBR10U200P513
Q3, Q4: GAN3R2-100CBEAZ; GAN3R2100CBEAZ
TP1, TP11: TestPoint; GanDapter Long pad
TP2, TP5: TestPoint; GanDapter short pad
TP3, TP12, TP13, TP14: TestPoint; GanDapter single pad

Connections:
/Synchronous Rectification/3: D1.3 (K), Q3.3 (D), Q3.5 (D), Q3.7 (D), TP1.1
/Synchronous Rectification/5: D2.3 (K), Q4.3 (D), Q4.5 (D), Q4.7 (D), TP11.1
GND: D1.1 (A_1), D1.2 (A_2), D2.1 (A_1), D2.2 (A_2), Q3.2 (S), Q3.4 (S), Q3.6 (S), Q3.8 (S), Q4.2 (S), Q4.4 (S), Q4.6 (S), Q4.8 (S), TP2.1, TP5.1, TP14.1
unnamed: Q4.1 (G), TP12.1
unnamed: Q3.1 (G), TP3.1

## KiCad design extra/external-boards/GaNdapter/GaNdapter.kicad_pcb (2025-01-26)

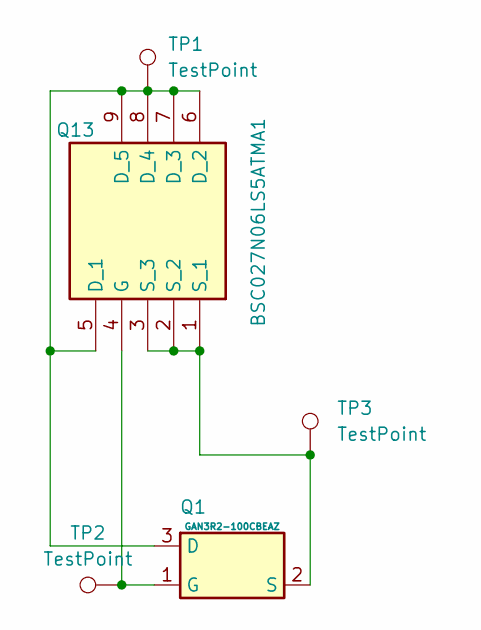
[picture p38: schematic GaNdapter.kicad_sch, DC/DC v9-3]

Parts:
Q1: GAN3R2-100CBEAZ; GAN3R2100CBEAZ; Mouser Part Number 771-GAN3R2-100CBEAZ
Q13: BSC027N06LS5ATMA1; Mouser Part Number 726-BSC027N06LS5ATMA
TP1: TestPoint; GanDapter Long pad
TP2: TestPoint; GanDapter single pad
TP3: TestPoint; GanDapter short pad

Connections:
unnamed: Q1.1 (G), Q13.4 (G), TP2.1
unnamed: Q1.3 (D), Q1.5 (D), Q1.7 (D), Q13.5 (D_1), Q13.6 (D_2), Q13.7 (D_3), Q13.8 (D_4), Q13.9 (D_5), TP1.1
unnamed: Q1.2 (S), Q1.4 (S), Q1.6 (S), Q1.8 (S), Q13.1 (S_1), Q13.2 (S_2), Q13.3 (S_3), TP3.1

Board: 2 copper layers, 5 parts (0 on the bottom side), 3 nets, no tracks yet.

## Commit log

2025-01-27 updated readme, removed copy of some pictures
    [DCDCv9-3.kicad_pcb]
2025-01-27 adjusted creepage distance
    The closest inner layer to outer layer, which uses a prepreg of 0.21 mm, would result in 0.81 mm creepage distance on edges. Due to unknown IPC 2221 rating for this case, the design was adjusted (bel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
    [DCDCv9-3.kicad_pcb, positions.csv]
2025-02-04 improved clearance on R54
    [DCDCv9-3.kicad_pcb, DCDCv9-3.kicad_sch]
2025-02-04 increased clearance a bit more
    [DCDCv9-3.kicad_pcb, DCDCv9-3.kicad_sch]
2025-02-11 increased distances on Coil formers
    Increased distances on Coil formers. Width changed from 22 mm to 26 so 2 mm more on each side. This increases creepage distance to at least 4 mm (realistically it's more than 6 mm) and adding more margin of error in case of looser coil winding. Center split width on the primary coil former was decreased from 0.9 to 0.8 mm to allow 0.05 mm more space for the primary
    [ETD39_prim.stl, ETD39_prim_Bank-winding_OLD.stl, ETD39_prim_plain_OLD.stl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]
2025-03-08 included LTspice simulation for precharge
    [DCDCv9-3.kicad_sch]
2025-03-08 updated PCBA BOM due to JLC error
    [bom_for_JLC_PCBA.csv, bom_for_JLC_PCBA.xls]
2025-03-16 fixed mixed up U_on/off comment at U6B, added PDF plot of schematic, replaced TL431 ED back to TL431
    [DCDCv9-3.kicad_sch]
2025-03-16 updated Readme.md with better formatting
    [DCDCv9-3.kicad_sch]
2025-03-17 added inductance calculator with air gap to table
    [DCDCv9-3_Table.ods, DCDCv9-3_Table.xlsx]
2025-03-20 added transformer calc for LTspice
    [DCDCv9-3_Table.ods, DCDCv9-3_Table.xlsx]
2025-04-23 updated bom, wrong 22uF cap for 0805 footprint
    [DCDCv9-3.kicad_sch, DCDCv9-3_kicad_full_bom.csv, DCDCv9-3_kicad_full_bom.xlsx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]
2025-05-01 fixed wrong gate charge in LTspice FET Model
    Ut was set to 2200 nC but should be 22 nC. Seems to not affect much in the simulation.
2025-05-04 LTSpice Models: wrong inductor resistance, changed 12V version capacitance
2025-05-17 Changed Mounting Holes from 2.9 mm to 3.0 mm
    Changed Mounting Holes from 2.9 mm to 3.0 mm. Although 2.9 mm was a nice fit for M3 screws, increasing it a bit will help against manufacturing tolerances.
    Note: The footprint originated from a M2.5 Footprint. Despite changing the diameter, the old name remained until now.
    Rules note: T 10.1.2 does not apply (Minimum M4), als the DCDC is not part of any primary structure. However, if somebody really needs M4, it is totally possible to increase the hole size by drilling - there is enough distance between the hole and traces. Just make sure that any screw heads are not shorting anything. The use of M4 pan head screws might therefore not be possible.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
    [DCDCv9-3.kicad_pcb]
2025-05-21 Update May 21 2025
    - Updated all Docs, for details see Revision History (new) on last page
    - added STEP files in addition to the STL for Transformer parts
    - fixed components on Mouser_BOM_for_PCBA despite being already placed on the PCBA, added UCC25600 for PCBA
    [DCDCv9-3_Mouser_BOM_for_PCBA.xlsx, DCDCv9-3_Table.ods, DCDCv9-3_Table.xlsx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]
2025-05-22 updated Table, see revision history on the first table page
    [DCDCv9-3_Table.ods, DCDCv9-3_Table.xlsx]
2025-06-11 Added note about not using 24 V on the output for testing
    Added note about not using 24 V on the output for testing due to the control loop shutting down the converter (which must happen - but is not useful for tests).
2025-06-19 Added R75 to lower the fan turn-on temperature
    Note: R75 (100k) is not added in the PCB design due to space restrictions. It is paralleled to R31 (4.7k) so the parallel value is around 4.49 k. The turn-on temperature is now 72°C and turn-off 58°C.
    The original design was measured to have 71°C/61°C on/off. However it was found that when mounted, the transformer could reach 90°C on the top without turning on the fan. A new measurement showed, th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
    [DCDCv9-3.kicad_pcb, DCDCv9-3.kicad_sch]
2025-06-23 updated Build guide
    Added notes about secondary coil being swapped and enable switch having too high resistance, added more details about IR-Thermometers measurement issues.
2025-06-29 Important update: Changed Gate Resistors
    R58 and R56 have been changed due to slight overvoltage. Deadtime must be increased to at least 150 ns (turn RV1 CCW). For more details see release notes DCDCv9-3r1.3
    [DCDCv9-3.kicad_pcb, DCDCv9-3.kicad_sch, DCDCv9-3_kicad_full_bom.csv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]
2025-07-05 Added WARNING to README (see issue), added Schematic as PDF
    Issue see: https://github.com/Rootthecause/DCDC/issues/8
2025-07-18 Important change regarding Git Issue #8
    Build Guide: Important change regarding Git Issue #8, replaced Plastik 70 with Plastik 70 Super.
    Datasheet: Added maximum internal low power control signal Voltage, Updated Troubleshooting from Build Guide (July 18, 2025)
2025-09-14 IMPORTANT NOTICE see #10 and fix in iBom
    IMPORTANT NOTICE: There was a complaint about the converter not being rules conform. Due to other personal priorities it might take some weeks to solve the addressed points. There is also the chance of some points unable to be resolved. See #10 for further details.
    iBom: There were some components missing in the iBom for PCBA.
    [DCDCv9-3.kicad_pcb, DCDCv9-3.kicad_sch, Synchronous Rectification.kicad_sch]
2025-09-28 fixed typo in schematic and README
    [DCDCv9-3.kicad_sch]
2026-03-10 updated build notes, added primary winding video
    [DCDCv9-3.kicad_sch, ETD39 Transformer Isolator 260308.stl, ETD39_prim_Bank-winding_OLD.stl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]
2026-03-14 large DCDCv9-3r1.4 release update
    - Removed some tables in csv and ods format (xlsx preferred)
    - fixed issue #10 (waiting for approval)
    - added video of adhesive testing for ESG10C-20G
    - added video of primary and secondary winding
    - updated all documentation files incl. Scrutineering Support Presentation
    - updated transformer isolator part
    - updated build notes
    - updated README.md
    - updated HV input connector
    - added note about the discontinuation of the German versions
    - added R75 onto the PCB (not required to solder on top of R31 anymore)
    - updated iBoms and comments
    - removed solder mask between TS an LV for better inspection
    - replaced J1, unified crimps for all molex housings
    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
    [DCDCv9-3.kicad_pcb, DCDCv9-3.kicad_sch, DCDCv9-3_Mouser_BOM_for_PCBA.csv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]
2026-03-24 Fixed TL431 LCSC part number, added single winding holder for 12V version
    [DCDCv9-3.kicad_sch, ETD39_sek_single_winding.step, ETD39_sek_single_winding.stl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]
2026-04-10 fixed R1, R71 wrong JLC component number for PCBAs see #13
    [bom.csv, bom_for_JLC_PCBA.xls]
2026-04-20 removed bug-causing comma in LTspice sim
    The Initial condition of the output capacitor was separated by a comma from it's capacitance value. This caused the simulation to fail on a Windows OS. As it also runs perfectly fine without the comma on MacOS, I removed it for all.
2026-05-11 Fixed U1 (see Build notes 260410), updated BOMs
    [DCDCv9-3.kicad_pcb, DCDCv9-3.kicad_sch, DCDCv9-3_Mouser_BOM_for_PCBA.xlsx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]
2026-05-16 added MP4581 as replacement for MP4541
    [DCDCv9-3.kicad_sch]
